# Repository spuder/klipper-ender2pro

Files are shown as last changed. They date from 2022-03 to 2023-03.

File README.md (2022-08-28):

# Klipper Ender 2 Pro

My clipper configuration for the ender 2 pro

[http://ender2pro.local/](http://ender2pro.local/)

## Hardware

- Ender 2 Pro (Purchased December 2021)
- Creality Silent board v4.2.3

## Mods

- [Raspberry Pi Case](https://github.com/spuder/ender2pro-raspberrypi)
- Mosfets on Fans
- [LED Bar](https://github.com/spuder/ender2pro-led-bracket)
- [Run out Sensor](https://www.amazon.com/gp/product/B08QJDP36R/ref=ppx_yo_dt_b_search_asin_title?ie=UTF8&psc=1)
- 12v Regulators on fans
- [BlTouch](https://github.com/spuder/ender2pro-bltouch)

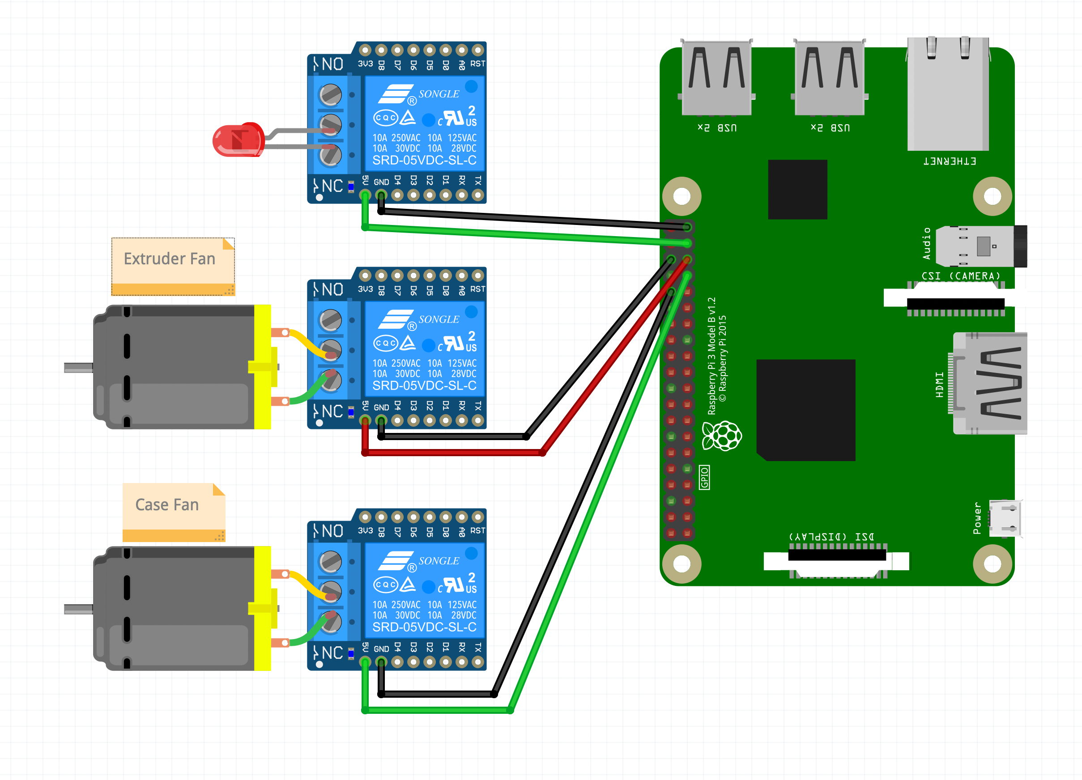
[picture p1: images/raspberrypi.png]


(See [RaspberryPi.fzz](./RaspberryPi.fzz) for schematic)

## Tuning

- https://teachingtechyt.github.io/calibration.html
- https://github.com/AndrewEllis93/Print-Tuning-Guide

### Input Shaper

Input shaper tools are installed with `playbooks/input_shaper.yaml`. The playbook can be called with the makefile shortcut `make input_shaper`

Files are copied from the host back to this repo

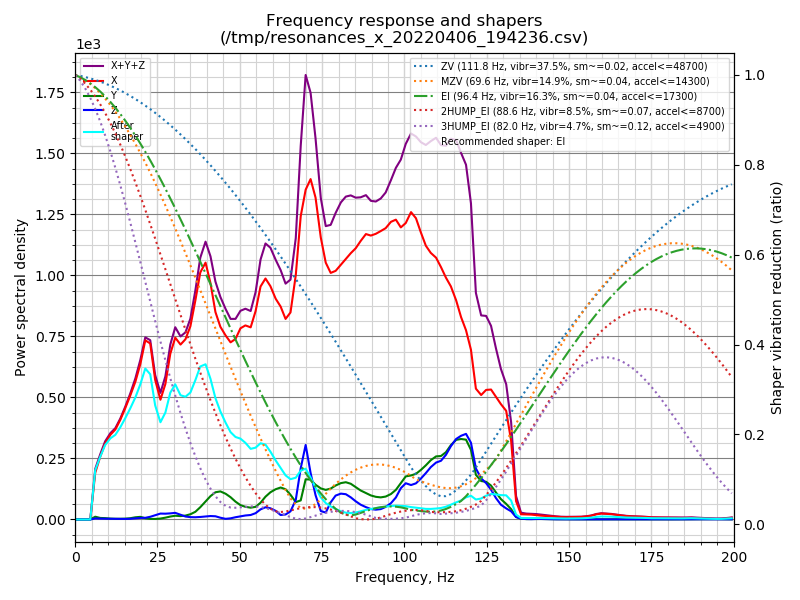
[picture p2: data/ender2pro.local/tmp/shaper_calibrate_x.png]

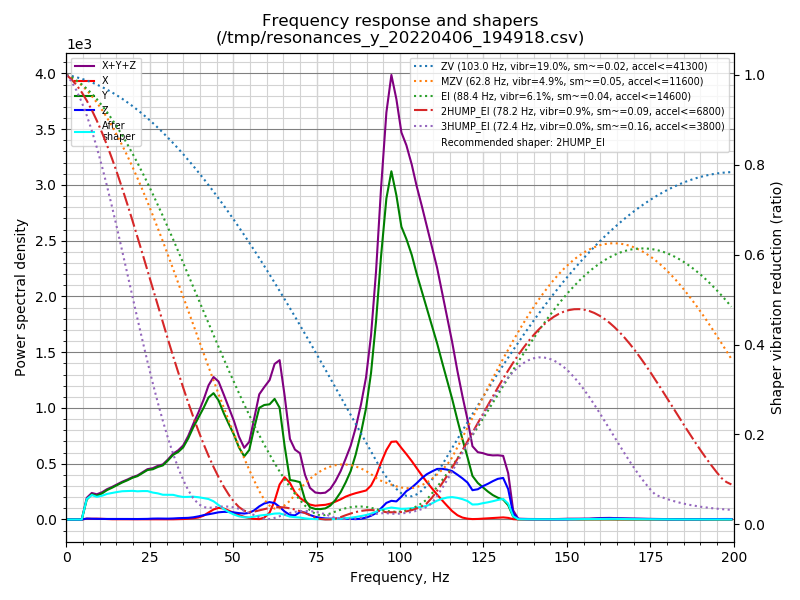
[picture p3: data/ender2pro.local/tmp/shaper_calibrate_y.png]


Recomended shaper settings are printed out with ansible

```
TASK [Print Calibrate Y] **********************************************************************************************************************
ok: [ender2pro.local] => {
    "msg": [
        "Fitted shaper 'zv' frequency = 103.0 Hz (vibrations = 19.0%, smoothing ~= 0.020)",
        "To avoid too much smoothing with 'zv', suggested max_accel <= 41300 mm/sec^2",
        "Fitted shaper 'mzv' frequency = 62.8 Hz (vibrations = 4.9%, smoothing ~= 0.052)",
        "To avoid too much smoothing with 'mzv', suggested max_accel <= 11600 mm/sec^2",
        "Fitted shaper 'ei' frequency = 88.4 Hz (vibrations = 6.1%, smoothing ~= 0.042)",
        "To avoid too much smoothing with 'ei', suggested max_accel <= 14600 mm/sec^2",
        "Fitted shaper '2hump_ei' frequency = 78.2 Hz (vibrations = 0.9%, smoothing ~= 0.088)",
        "To avoid too much smoothing with '2hump_ei', suggested max_accel <= 6800 mm/sec^2",
        "Fitted shaper '3hump_ei' frequency = 72.4 Hz (vibrations = 0.0%, smoothing ~= 0.156)",
        "To avoid too much smoothing with '3hump_ei', suggested max_accel <= 3800 mm/sec^2",
        "Recommended shaper is 2hump_ei @ 78.2 Hz"
    ]
}
```

### BLTOUCH

A BLTouch is installed.

**Warning**: There are 2 ways to install the BLTouch on a Creality silent board. This assumes using a single 5 pin header instead of separate 2 pin and 3 pin headers. If you don't know the difference, see [timestamp 7:24 in this youtube video by teaching tech](https://youtu.be/eF060dBEnfs?t=444)

##3 Fillament runout sensor

The following part plugs directly into the `Pre-srt Port` on creality board 4.2.2 / 4.2.3





- Part: https://www.amazon.com/gp/product/B08QJDP36R/ref=ppx_yo_dt_b_search_asin_title?ie=UTF8&psc=1

#### klipper runout sensor config

The following will just work on klipper, assuming you already have a 'pause' and 'resume' macro defined. 

As soon as the fillament runs out, it will pause the print. To resume, click the 'resume' macro in the gui

```
[filament_switch_sensor RunoutSensor]
pause_on_runout: True
switch_pin: !PA4
```

If you wish to override the runout sensor with your own macro, you can specify it like so
```
[filament_switch_sensor RunoutSensor]
pause_on_runout: True
switch_pin: !PA4
runout_gcode: PAUSE
insert_gcode: RESUME
```

### Bed Mesh

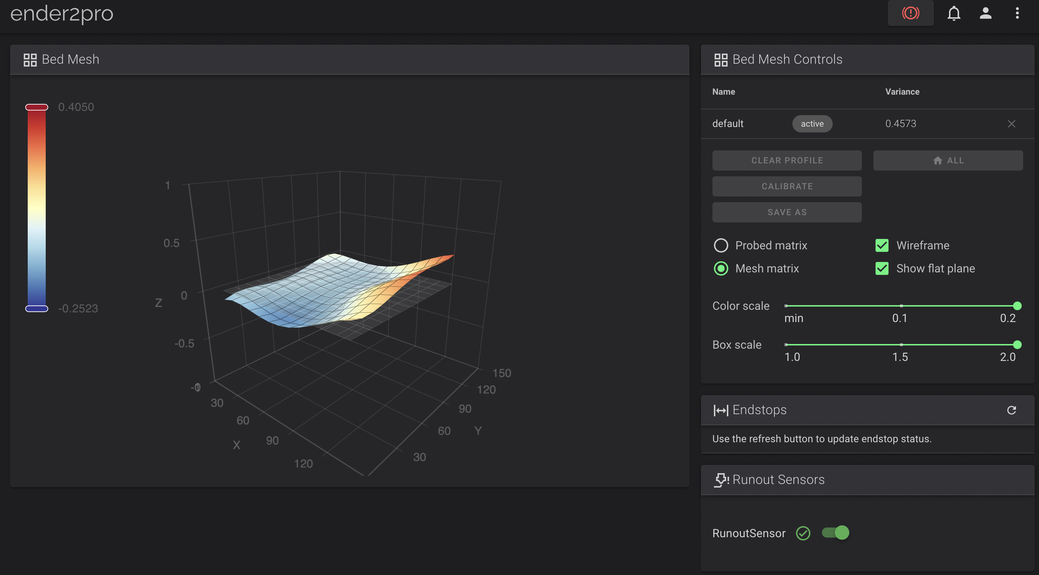
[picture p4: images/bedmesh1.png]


Run this command to run a bed mesh calibration, then save it for future use

```
BED_MESH_CALIBRATE PROFILE=PEI
SAVE_CONFIG
```

The mesh will then be saved to the printer.cfg. **Be sure to copy it back to this repo or changes will be lost**

Open the printer.cfg in fluidd/mainsail and look for lines that start with:
```
#*# <---------------------- SAVE_CONFIG ---------------------->
#*# DO NOT EDIT THIS BLOCK OR BELOW. The contents are auto-generated.
```

### Setup

The following settings are for a Creality Silent board v4.2.2
```
make menuconfig
# SM32F103
# 28KiB bootloader
# Disable usb for communication
make
# Then copy the .bin file off the raspberry pi and put it on a fresh SD Card.
# The .bin file must be named something unique (and it can't be firmware.bin, or the previous file name)
````

### Resources

- Pinout: https://docs.google.com/spreadsheets/d/1DYhh9fwLnvZzuNvMoBen9Dl68KN-4TWkbO94lJ4iwe4/edit

- https://www.youtube.com/watch?v=MaUU8stsZPo
- https://www.youtube.com/watch?v=ABsdnkP4iwQ
- 4.2.7 pinout https://all3dp.com/2/klipper-ender-3-v2/
- 4.2.7 pinout https://3dprinting.stackexchange.com/questions/16078/steppers-stuck-with-klipper-but-work-with-marlin
- 4.2.7 klipper config https://github.com/Klipper3d/klipper/pull/3335/files
- Install on Ender 3 V2 https://www.youtube.com/watch?v=gfZ9Lbyh8qU
- Klipper Support https://github.com/spuder/klipper/pull/1/files

## Extruder Calibration

- https://3dprintbeginner.com/extruder-calibration-guide/

## Flow Calibration

- https://3dprintbeginner.com/flow-rate-calibration/

## OS setup

To setup the OS

1. Download FluidPI: https://github.com/fluidd-core/FluiddPI
2. Download Raspbery Pi imageer https://www.raspberrypi.com/software/
3. Press cmd+shift+x to get advanced settings.
4. Change the hostname to `ender2pro` (or whatever you want. It must match ansible inventory file)
5. Use ansible/make to configure

## Ansible

klipper config file is located at `/home/{{ user }}/klipper_config/printer.cfg`
This repo contains an ansible playbook that will copy the local printer.cfg to the printer and restart the klipper service if it changes. 

To use
1. Modify `inventory` to point at your raspberry pi
2. Run the following ansible commands (Or use the make shortcuts)

Setup ssh keys
```
ssh-copy-id -i ~/.ssh/id_rsa.pub pi@ender2pro.local
```

```
ansible-playbook --check playbook.yaml
ansible-playbook -i inventory playbook.yaml -c paramiko --ask-pass
```

For best results, use the default user 'pi'. If you change it, you will need to manually update all the init scripts since they are hard coded to `/home/pi/*`

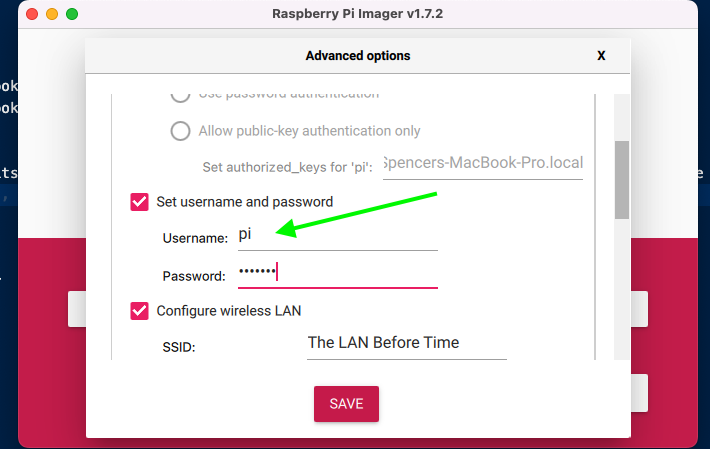
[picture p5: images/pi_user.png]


```
make klipper    # run just the klipper playbook (default)
make moonraker  # run just the moonraker playbook
make webcam     # run just the webcam playbook
make all        # run all playbooks
make            # runs default (in this case klipper)
```

Then navigate to [http://ender2pro.local/#/](http://ender2pro.local/#/) and enjoy

## UART vs USB

If using the UART cable instead of the USB cable, you need to run additional steps

https://github.com/Klipper3d/klipper/blob/master/docs/RPi_microcontroller.md#install-the-rc-script

1. Recompile klipper firmware to use UART not USB
2. Install the klipper_mcu init script
3. run `make flash` and select linux process
4. Restart klipper

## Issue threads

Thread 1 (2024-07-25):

Result speeds

juan518munoz, 2024-07-25:
I'm looking into adding klipper to an Ender 2 Pro and was wondering what speeds are achievable after doing modifications like you did.

spuder, 2024-07-25:
I don't have exact numbers, however the hotend can't pump out enough heat to get very fast. You might want to upgrade the nozzle.

juan518munoz, 2024-07-25:
Did you try anything around 100 mm/s? If so, with what acceleration value?

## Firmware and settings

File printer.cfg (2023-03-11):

[include macros/*.cfg]

[stepper_x]
step_pin: PC2
dir_pin: PB9
enable_pin: !PC3
microsteps: 16
rotation_distance: 40
endstop_pin: ^PA5
position_min: -11
position_endstop: -11
position_max: 165
homing_speed: 50

[stepper_y]
step_pin: PB8
dir_pin: PB7
enable_pin: !PC3
microsteps: 16
rotation_distance: 40
endstop_pin: ^PA6
position_min: -5
position_endstop: -5
position_max: 165
homing_speed: 50

[stepper_z]
step_pin: PB6
dir_pin: !PB5
enable_pin: !PC3
microsteps: 16
rotation_distance: 8
endstop_pin: probe:z_virtual_endstop
position_min: -5.0
position_max: 180

[extruder]
max_extrude_only_distance: 100.0
step_pin: PB4
dir_pin: PB3
enable_pin: !PC3
microsteps: 16
rotation_distance: 27.53480577
nozzle_diameter: 0.400
filament_diameter: 1.750
heater_pin: PA1
sensor_pin: PC5
sensor_type: EPCOS 100K B57560G104F
control: pid
# PID_CALIBRATE HEATER=extruder TARGET=220
pid_Kp: 29.492
pid_Ki: 2.070
pid_Kd: 105.067
min_temp: 0
max_temp: 260

[heater_bed]
heater_pin: PB10
sensor_type: EPCOS 100K B57560G104F
sensor_pin: PC4
control: pid
# PID_CALIBRATE HEATER=heater_bed TARGET=50
pid_Kp: 72.921
pid_Ki: 1.594
pid_Kd: 834.031
min_temp: 0
max_temp: 85

# Part Cooling Fan
[fan]
pin: PA0

[mcu]
serial: /dev/serial/by-id/usb-1a86_USB_Serial-if00-port0
restart_method: command

[temperature_sensor raspberry_pi]
sensor_type: temperature_host
max_temp: 100

[temperature_sensor mcu_temp]
sensor_type: temperature_mcu #Spider Temps
max_temp: 100

# Make sure you add the klipper init script for the mcu
# https://github.com/Klipper3d/klipper/blob/master/docs/RPi_microcontroller.md#install-the-rc-script
[mcu rpi]
serial: /tmp/klipper_host_mcu

# Accelerometer
[adxl345]
cs_pin: rpi:None

[resonance_tester]
accel_chip: adxl345
probe_points:
    83, 83, 20

[printer]
kinematics: cartesian
max_velocity: 300
max_accel: 6800 # Calculated from input_shaper https://www.klipper3d.org/Measuring_Resonances.html
max_z_velocity: 5
max_z_accel: 100

# https://github.com/MarlinFirmware/Configurations/pull/633#issuecomment-995424611
# https://docs.google.com/spreadsheets/d/1DYhh9fwLnvZzuNvMoBen9Dl68KN-4TWkbO94lJ4iwe4/edit
[display]
lcd_type: st7920
cs_pin: PB12
sclk_pin: PB13
sid_pin: PB15
encoder_pins: ^PB14, ^PA2
click_pin: ^!PB2

[output_pin beeper]
pin: PC6

# Calibrated for this bracket https://www.thingiverse.com/thing:5176711
[bltouch]
sensor_pin: ^PB1
control_pin: PB0
x_offset: -30
y_offset: 2
z_offset: 1.830 # PROBE_CALIBRATE

# BLTouch home location
[safe_z_home]
home_xy_position: 83, 63 # Change coordinates to the center of your print bed
speed: 50
z_hop: 10
z_hop_speed: 20

[virtual_sdcard]
path: /home/pi/printer_data/gcodes

# TUNING_TOWER COMMAND='SET_HEATER_TEMPERATURE HEATER=extruder' PARAMETER=TARGET START=235 FACTOR=-1 BAND=10.0
[tuning_tower]

[pause_resume]

[idle_timeout]
timeout: 600

[duplicate_pin_override]
pins: PC5, rpi:LED_BAR

[board_pins]
mcu: rpi
aliases:
    CASE_FAN=gpio13,    #BCM=13, wPI=23, Physical=33 (green/black long)
    EXTRUDER_FAN=gpio19,#BCM=19, wPI=24, Physical=35 (red/blue)
    LED_BAR=gpio26      #BCM=26, wPI=25, Physical=37 (green/black short)

[heater_fan extruder]
pin: rpi:EXTRUDER_FAN
heater: extruder
fan_speed: 1.0

[controller_fan case_fan]
pin: rpi:CASE_FAN
fan_speed: 1.0 # Fan is too loud at 100%, but the PWM signal is very anoying
heater: heater_bed

# https://www.thingiverse.com/thing:5176620
[output_pin led_bar]
pin: rpi:LED_BAR

# BED_SCREWS_ADJUST
[bed_screws]
screw1: 26, 32
screw2: 136, 32
screw3: 136, 126
screw4: 26, 126

# https://www.klipper3d.org/Manual_Level.html#adjusting-bed-leveling-screws-using-the-bed-probe
# G28
# SCREWS_TILT_CALCULATE
[screws_tilt_adjust]
screw1: 57, 38
screw1_name: front left screw
screw2: 165, 38
screw2_name: front right screw
screw3: 165, 132
screw3_name: back right screw
screw4: 57, 132
screw4_name: back left screw


# BED_MESH_CALIBRATE PROFILE=default
[bed_mesh]
speed: 120
horizontal_move_z: 5
mesh_min: 10,10
mesh_max: 130, 130
probe_count: 7,7
algorithm: bicubic


[filament_switch_sensor RunoutSensor]
pause_on_runout: True
switch_pin: !PA4


# Input Shaper
[input_shaper]
shaper_freq_x: 96.4
shaper_type_x: ei
shaper_freq_y: 78.2
shaper_type_y: 2hump_ei

# BED_MESH_CALIBRATE PROFILE=default
# The following config is saved by the bed mesh leveling

#*# <---------------------- SAVE_CONFIG ---------------------->
#*# DO NOT EDIT THIS BLOCK OR BELOW. The contents are auto-generated.
#*#
#*# [bed_mesh default]
#*# version = 1
#*# points =
#*# 	-0.032500, -0.052500, 0.000000, -0.050000, -0.012500, 0.107500, 0.275000
#*# 	-0.037500, -0.062500, -0.022500, -0.077500, -0.032500, 0.060000, 0.242500
#*# 	0.052500, -0.075000, 0.022500, -0.027500, -0.012500, 0.080000, 0.252500
#*# 	-0.082500, -0.077500, -0.007500, -0.050000, -0.027500, 0.057500, 0.257500
#*# 	-0.007500, -0.045000, -0.372500, -0.047500, 0.007500, 0.110000, 0.265000
#*# 	0.017500, -0.022500, 0.002500, -0.032500, -0.025000, 0.060000, 0.272500
#*# 	0.165000, -0.047500, 0.012500, -0.040000, -0.015000, 0.095000, 0.230000
#*# tension = 0.2
#*# min_x = 10.0
#*# algo = bicubic
#*# y_count = 7
#*# mesh_y_pps = 2
#*# min_y = 10.0
#*# x_count = 7
#*# max_y = 130.0
#*# mesh_x_pps = 2
#*# max_x = 130.0
#*#
#*# [bltouch]
#*# z_offset = 1.830

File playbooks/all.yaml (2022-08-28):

---
- name: all
  hosts: ender2pro
  remote_user: pi
  gather_facts: no
  become: yes
  become_user: root
  


- name: klipper
  import_playbook: ./klipper_config.yaml
- name: moonraker
  import_playbook: ./moonraker_config.yaml
- name: webcam
  import_playbook: ./webcam_config.yaml
- name: input_shaper
  import_playbook: ./input_shaper.yaml

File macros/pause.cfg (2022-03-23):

######################################################################
# Pause Print
######################################################################

[gcode_macro PAUSE]
description: Pause the actual running print
rename_existing: PAUSE_BASE
# change this if you need more or less extrusion
variable_extrude: 1.0
gcode:
  CLEAR_PAUSE
  ##### read E from pause macro #####
  {% set E = printer["gcode_macro PAUSE"].extrude|float %}
  ##### set park positon for x and y #####
  # default is your max posion from your printer.cfg
  {% set x_park = printer.toolhead.axis_maximum.x|float - 5.0 %}
  {% set y_park = printer.toolhead.axis_maximum.y|float - 5.0 %}
  ##### calculate save lift position #####
  {% set max_z = printer.toolhead.axis_maximum.z|float %}
  {% set act_z = printer.toolhead.position.z|float %}
  {% if act_z < (max_z - 2.0) %}
      {% set z_safe = 2.0 %}
  {% else %}
      {% set z_safe = max_z - act_z %}
  {% endif %}
  ##### end of definitions #####
  PAUSE_BASE
  G91
  {% if printer.extruder.can_extrude|lower == 'true' %}
    G1 E-{E} F2100
  {% else %}
    {action_respond_info("Extruder not hot enough")}
  {% endif %}
  {% if "xyz" in printer.toolhead.homed_axes %}
    G1 Z{z_safe} F900
    G90
    G1 X{x_park} Y{y_park} F6000
  {% else %}
    {action_respond_info("Printer not homed")}
  {% endif %} 

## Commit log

2022-03-16 add configs
    [printer.cfg]
2022-03-16 pause resume
    [printer.cfg]
2022-03-17 use heater
    [printer.cfg]
2022-03-18 Add more configs
    [macros.cfg, printer.cfg]
2022-03-18 add cfgs
    [fillament_change.cfg, macros.cfg, pause.cfg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]
2022-03-18 split tasks
    [led.cfg, printer.cfg]
2022-03-18 comment out stuff
    [led.cfg]
2022-03-18 Add more examples
    [led.cfg]
2022-03-20 working led
    [led.cfg, macros.cfg, printer.cfg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]
2022-03-20 bed mesh level
    [printer.cfg]
2022-03-22 add temp sensor
    [printer.cfg]
2022-03-25 bed level
    [printer.cfg]
2022-03-25 adjust screws
    [printer.cfg]
2022-03-25 bed mesh bicubic
    [printer.cfg]
2022-03-25 z calibrate
    [printer.cfg]
2022-04-06 add accelerometer
    [printer.cfg]
2022-04-07 input shaper
    [printer.cfg]
2022-08-12 use raspberry pi imagr
2022-08-28 Add docs
    [RaspberryPi.fzz]
2023-03-11 update configs
    [printer.cfg]
